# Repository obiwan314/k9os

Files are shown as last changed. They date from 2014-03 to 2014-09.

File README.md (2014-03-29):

k9os
====

A collection of software to control a Raspberry PI based K9 robot.

This is a hardware/software project in progress that is documented on my blog at http://gwfrontiers.blogspot.com.

This project is intended to be checked out on your raspberry pi.
Once this is done run:

cd bin
sudo ./install.sh

This will install the Arduino scripts into the required locations and install and configure the k9os daemon for interfacing over USB to the two arduinos used to control the robot.

This is a personal research project and any sourcecode or hardware designs are provided here without any warrenty or gaurentee.

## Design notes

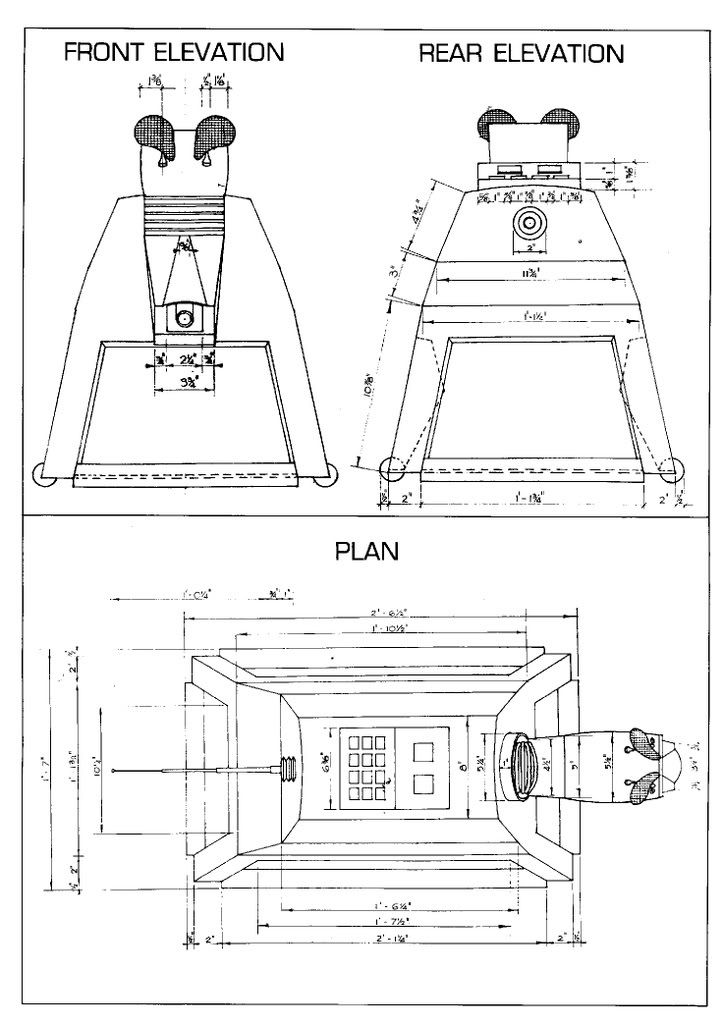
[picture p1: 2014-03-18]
hardware/exterior/k9_views.jpeg

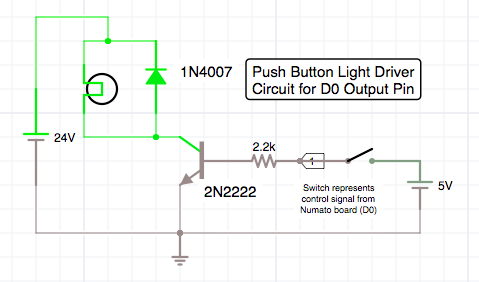
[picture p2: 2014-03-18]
hardware/simulations/light_driver.png

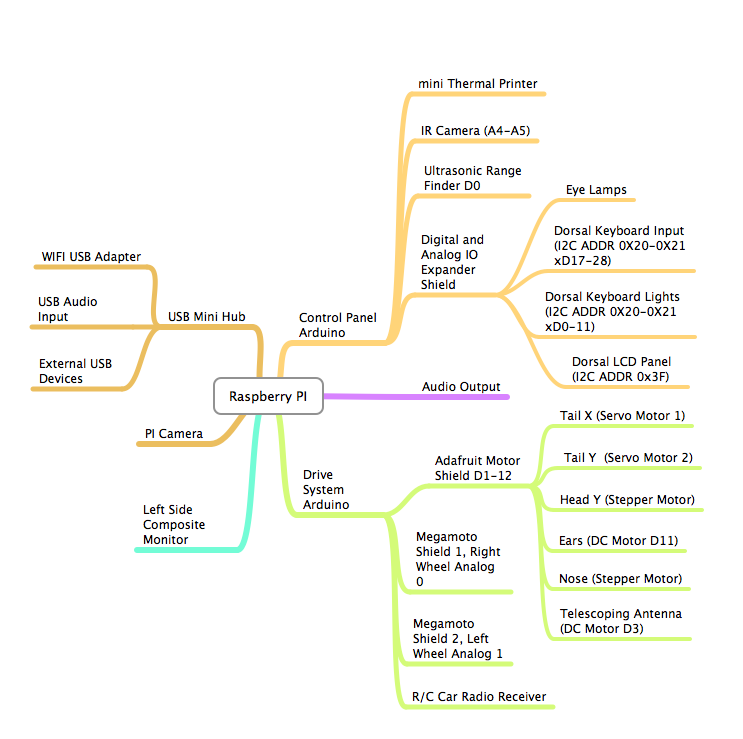
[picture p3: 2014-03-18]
hardware/architecture/system_overview.png

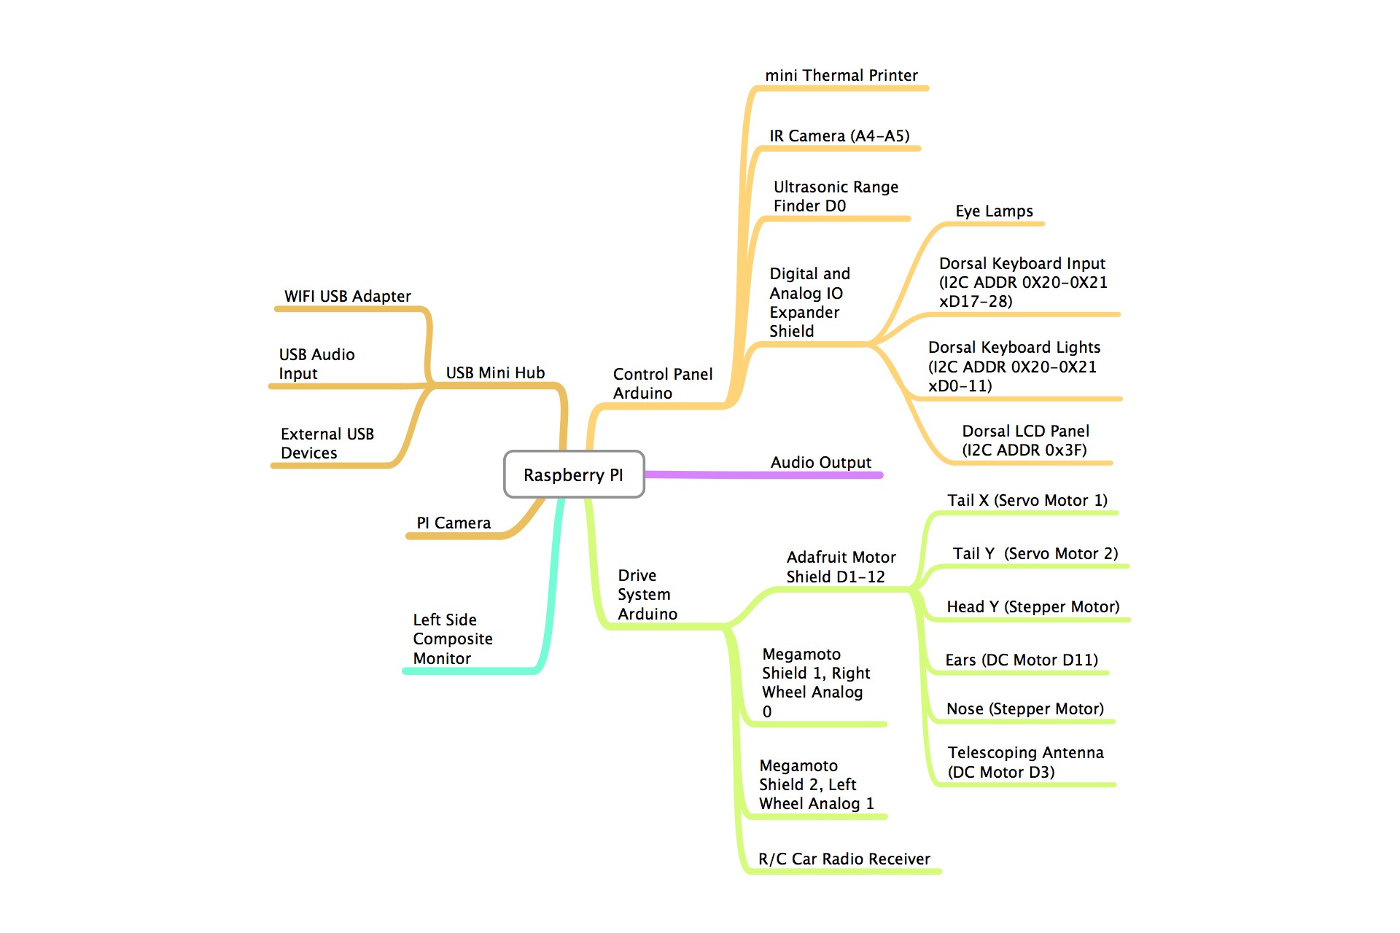
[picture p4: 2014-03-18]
hardware/architecture/system_overview.mindnode/QuickLook/Preview.jpg

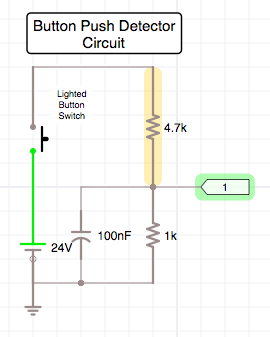
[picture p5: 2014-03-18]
hardware/simulations/switch_controller.png

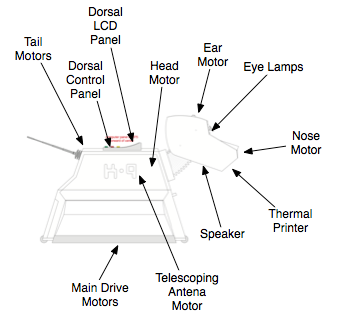
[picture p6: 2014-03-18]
hardware/exterior/right_side.png

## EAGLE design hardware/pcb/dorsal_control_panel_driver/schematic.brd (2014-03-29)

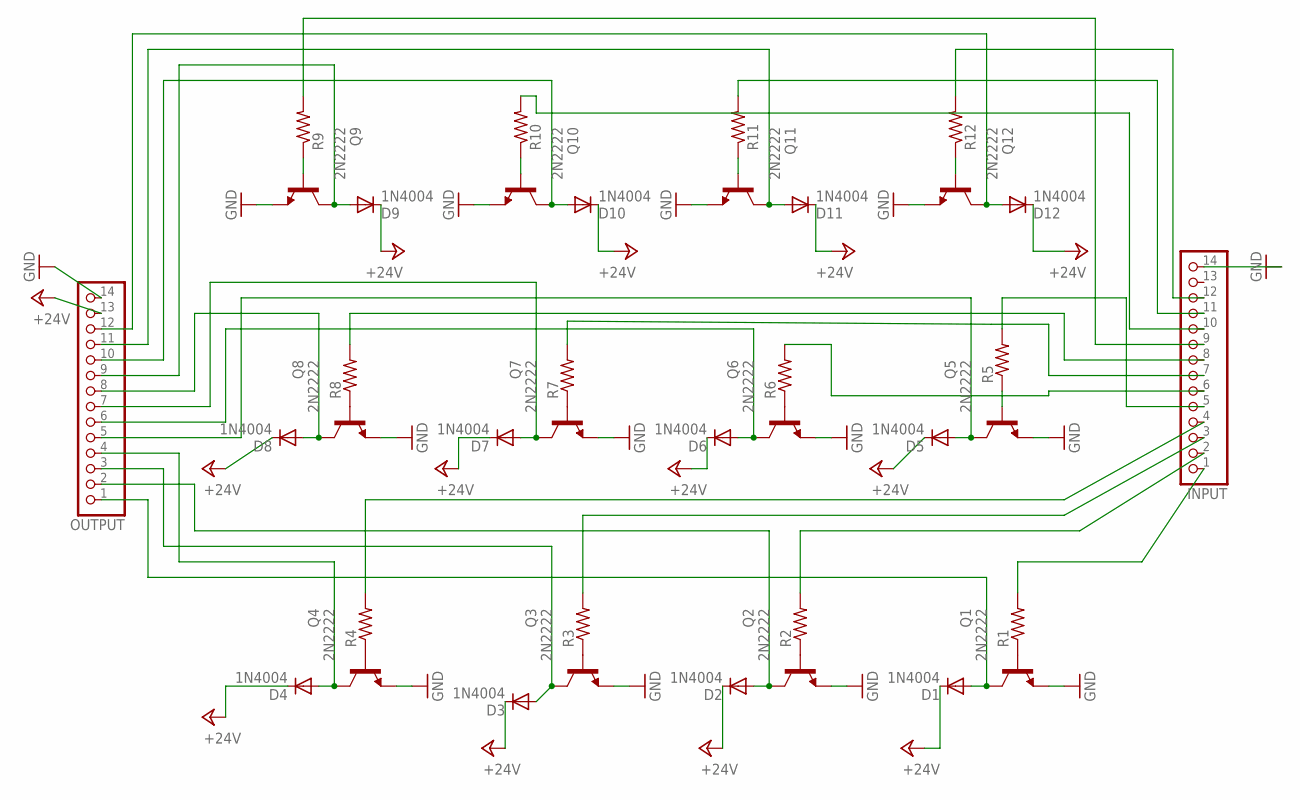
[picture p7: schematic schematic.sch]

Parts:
D1, D2, D3, D4, D5, D6, D7, D8, D9, D10, D11, D12: 1N4004; DO41-10; MPN 1N4004
INPUT: PINHD-1X14; 1X14
OUTPUT: PINHD-1X14; 1X14
Q1, Q2, Q3, Q4, Q5, Q6, Q7, Q8, Q9, Q10, Q11, Q12: 2N2222; TO92-EBC-OVAL; MPN PN2222ATF
R1, R2, R3, R4, R5, R6, R7, R8, R9, R10, R11, R12: R-US_0309/12; 0309/12

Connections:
+24V: D1.C, D2.C, D3.C, D4.C, D5.C, D6.C, D7.C, D8.C, D9.C, D10.C, D11.C, D12.C, OUTPUT.13
GND: INPUT.14, OUTPUT.14, Q1.E, Q2.E, Q3.E, Q4.E, Q5.E, Q6.E, Q7.E, Q8.E, Q9.E, Q10.E, Q11.E, Q12.E
unnamed: D1.A, OUTPUT.1, Q1.C
unnamed: Q1.B, R1.1
unnamed: INPUT.1, R1.2
unnamed: D2.A, OUTPUT.2, Q2.C
unnamed: Q2.B, R2.1
unnamed: INPUT.2, R2.2
unnamed: D3.A, OUTPUT.3, Q3.C
unnamed: Q3.B, R3.1
unnamed: INPUT.3, R3.2
unnamed: D4.A, OUTPUT.4, Q4.C
unnamed: Q4.B, R4.1
unnamed: INPUT.4, R4.2
unnamed: D5.A, OUTPUT.5, Q5.C
unnamed: Q5.B, R5.1
unnamed: INPUT.5, R5.2
unnamed: D6.A, OUTPUT.6, Q6.C
unnamed: Q6.B, R6.1
unnamed: INPUT.6, R6.2
unnamed: D7.A, OUTPUT.7, Q7.C
unnamed: Q7.B, R7.1
unnamed: INPUT.7, R7.2
unnamed: D8.A, OUTPUT.8, Q8.C
unnamed: Q8.B, R8.1
unnamed: INPUT.8, R8.2
unnamed: D9.A, OUTPUT.9, Q9.C
unnamed: Q9.B, R9.1
unnamed: INPUT.9, R9.2
unnamed: D10.A, OUTPUT.10, Q10.C
unnamed: Q10.B, R10.1
unnamed: INPUT.10, R10.2
unnamed: D11.A, OUTPUT.11, Q11.C
unnamed: Q11.B, R11.1
unnamed: INPUT.11, R11.2
unnamed: D12.A, OUTPUT.12, Q12.C
unnamed: Q12.B, R12.1
unnamed: INPUT.12, R12.2

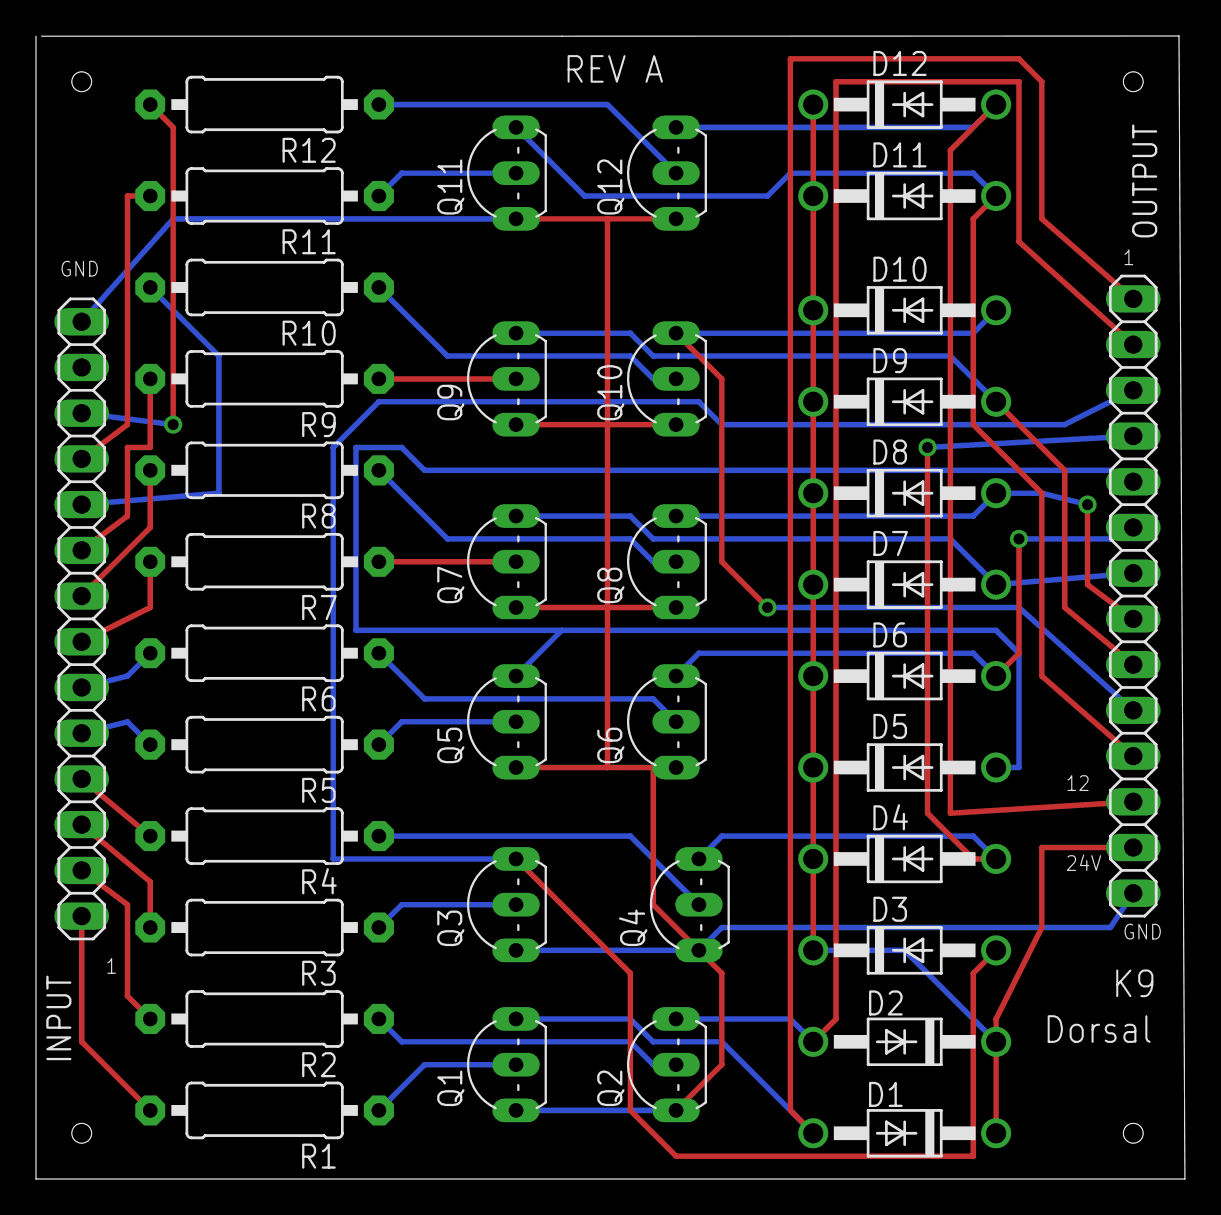
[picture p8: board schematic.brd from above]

Board: 2 copper layers, 63.8 x 63.5 mm, 38 parts (0 on the bottom side), 38 nets.

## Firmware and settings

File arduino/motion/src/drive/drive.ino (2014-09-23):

#include <Servo.h>

/*
 * K9OS drive motor sketch
 * Controls Scooter Motors,
 * Compass, RC Receiver and
 * Ultrasonic Rangefinder
 */

#include <Wire.h> //I2C Arduino Library
#include <math.h>
#include <aJSON.h>

const float pi=3.14159;

// Megamoto Resources
int EnablePin = 8;
int PWMPin = 11;  // Timer2
int PWMPin2 = 3;
int PWMPinA = 9;  // Timer2
int PWMPinA2 = 10;
const int DIRECTION_FORWARD=1;
const int DIRECTION_BACKWARD=-1;
const int DIRECTION_STOP=0;
const int SPEED_STOP=0;
const int SPEED_SLOW=20;
const int SPEED_FAST=40;
const int SPEED_FASTER=60;
const int SPEED_FASTEST=70;
const int SPEED_RIDICULOUS=70;
const int SPEED_LUDICROUS=80;
const int NO_ROTATION=0;
const int LEFT_ROTATION=1;
const int RIGHT_ROTATION=-1;
const int SAFE_DISTANCE=15;

// Compass Constants
const int compassI2CAddress=0x1E;

// Remote Control
const int ultrasonicRangeFinderPin= 4;

// Globals
float lastHeading=-2;
float lastRange=-1;
float persistantBias=0;
int persistantDirection=0;
int persistantSpeed=0;
int persistantRotation=0;
int safetyStop=0;

void setup() {
  // Megamoto
  // initialize the digital pin as an output.
  // Pin 13 has an LED connected on most Arduino boards:
  pinMode(EnablePin, OUTPUT);
  pinMode(PWMPin, OUTPUT);
  pinMode(PWMPin2, OUTPUT);
  pinMode(PWMPinA, OUTPUT);
  pinMode(PWMPinA2, OUTPUT);
  setPwmFrequency(PWMPin, 1);  // change Timer2 divisor to 8 gives 3.9kHz PWM freq
  setPwmFrequency(PWMPinA, 1);  // change Timer2 divisor to 8 gives 3.9kHz PWM freq

  // Remote Control
  pinMode(5, INPUT); // Set our input pins as such
  pinMode(6, INPUT);
  pinMode(7, INPUT);
  pinMode(2, INPUT);

  // Set up compass
  Wire.begin();

  // Put the HMC5883 IC into the correct operating mode
  Wire.beginTransmission(compassI2CAddress); //open communication with HMC5883
  Wire.write(0x02); //select mode register
  Wire.write(0x00); //continuous measurement mode
  Wire.endTransmission();

  Serial.begin(115200); // Establish connection with raspberri pi 115200

}

void loop() {

  processReceivedMessages();
  int currentRange=echoRangeFinder();
  if(abs(lastRange-currentRange)>1){
    Serial.print("{\"onRangeChange\":");
    Serial.print(currentRange);
    Serial.println("}");
    lastRange=currentRange;
  }

  float heading=readHeading();
  if(abs(lastHeading-heading)>=2){
    Serial.print("{\"onHeadingChange\":");
    Serial.print(heading);
    Serial.println("}");
    lastHeading=heading;
  }
  
  processRcTransmitter(currentRange);

}

/**
 * Map RC receiver values to motor control 
 *  actions.
 */
void processRcTransmitter(int currentRange){
  // poll current RC receiver values
  int ch1 = pulseIn(5, HIGH, 25000); // B Switch, Disables everything
  int ch2 = pulseIn(6, HIGH, 25000); // B Stick vertical
  int ch3 = pulseIn(7, HIGH, 25000); // B Stick horizontal
  int ch4 = pulseIn(2, HIGH, 25000); // A Stick horizontal
  float bias=0;

  // Special case, in place rotation
  if(ch2>=1450&&ch2<1500){    
    // throttle at zero
    if(ch4<=1450){ // Spin Left
       controlMotor( 120,DIRECTION_FORWARD,0,LEFT_ROTATION);
       return;
    } else if(ch4>=1500){ // Spin Right
       controlMotor(120,DIRECTION_FORWARD,0,RIGHT_ROTATION);
       return;
    }     
  }
  
  // Calculate current bias
  if(ch4<1500&&ch4>1490)
    bias=0;
  if(ch4<=1490)
    bias=-((ch4-1490)/190.0)*0.8;
  if(ch4>=1500)
    bias=((ch3-1500)/200.0)*0.8;

  
  if(ch1<996){ // This sets SWB as the master motor cut off
      // Master cutoff switch is on or remote is off, autonomous behavior permitted
      if(persistantSpeed>0) {
          // We are moving autonomously
          if(currentRange<SAFE_DISTANCE&&persistantDirection==DIRECTION_FORWARD){
              // Shut down forward motion in from of an obsticle
              controlMotor(0,0,bias,NO_ROTATION);
              if(safetyStop==0){
                 Serial.println("{\"safetystop\":true}");
                 safetyStop=1;
              } 
              return;
          } else {
              // Execute raspberry pi commands if no remote is available and no obsticles present
              controlMotor(persistantSpeed,persistantDirection,persistantBias,persistantRotation);
              return;
          }
      }
   } else {
       // We are in remote control mode
       
       // Reverse
       if(ch2<1400){
          controlMotor(SPEED_FASTER,DIRECTION_BACKWARD,0,NO_ROTATION);
          return;
       }
       if(ch2>=1400&&ch2<1425){
          controlMotor(SPEED_FAST,DIRECTION_BACKWARD,0,NO_ROTATION);
          return;
        }
        if(ch2>=1425&&ch2<1450){
          controlMotor(SPEED_SLOW,DIRECTION_BACKWARD,0,NO_ROTATION);
          return;
        }
        
        // Stop
        if(ch2>=1450&&ch2<1500){
          controlMotor(SPEED_STOP,DIRECTION_STOP,0,NO_ROTATION);
          return;
        }
        
        // Forward
        if(currentRange>SAFE_DISTANCE){
            safetyStop=0;
            if(ch2>=1500&&ch2<1525){
                controlMotor(SPEED_SLOW,DIRECTION_FORWARD,0,NO_ROTATION);
                return;
            }
            if(ch2>=1525&&ch2<1550){
                controlMotor(SPEED_FAST,DIRECTION_FORWARD,0,NO_ROTATION);
                return;
             }
             if(ch2>=1550&&ch2<1575){
                controlMotor(SPEED_FASTER,DIRECTION_FORWARD,0,NO_ROTATION);
                return;
             }
             if(ch2>=1575&&ch2<1600){
                controlMotor(SPEED_FASTEST,DIRECTION_FORWARD,0,NO_ROTATION);
                return;
             }
             if(ch2>=1600&&ch2<1625){
                controlMotor(SPEED_RIDICULOUS,DIRECTION_FORWARD,0,NO_ROTATION);
                return;
             }
             if(ch2>=1625){
                controlMotor(SPEED_LUDICROUS,DIRECTION_FORWARD,0,NO_ROTATION);
                return;
             }
        } else {
              if(safetyStop==0){
                 Serial.println("{\"safetystop\":true}");
                 safetyStop=1;
              } 
             controlMotor(SPEED_STOP,DIRECTION_STOP,0,NO_ROTATION);
        }
  } // end remote control Mode

}

static inline int8_t sgn(int val) {
  if (val < 0) return -1;
  if (val==0) return 0;
  return 1;
}

void controlMotor(int speed,int direction,float bias,int rotate){
  int biasSpeedL=0.0;
  int biasSpeedR=0.0;
  if(bias==0){
    biasSpeedR=speed;
    biasSpeedL=speed;
  } else {
    if(bias*sgn(-direction)>0){
      biasSpeedL=abs(round(speed*bias));
      biasSpeedR=abs(round(speed*(1.0-bias)));
    } else {
      biasSpeedR=abs(round(speed*bias));
      biasSpeedL=abs(round(speed*(1.0-bias)));
    }
  }
//  Serial.print("bias=");Serial.println(bias);
//  Serial.print("Speed=");Serial.println(speed);
//  Serial.print("L=");Serial.println(biasSpeedL);
//  Serial.print("R=");Serial.println(biasSpeedR);
  if(rotate==0){
    if(direction==0){
      // Stop the motor fast
      speed=0;
      analogWrite(PWMPin, 0);
      analogWrite(PWMPinA, 0);
      analogWrite(PWMPin2, 0);
      analogWrite(PWMPinA2, 0);
      digitalWrite(EnablePin, LOW);
    } if(direction>0){
      // Forward
      analogWrite(PWMPin, biasSpeedL);
      analogWrite(PWMPinA, biasSpeedR);
      analogWrite(PWMPin2, 0);
      analogWrite(PWMPinA2, 0);
      digitalWrite(EnablePin, HIGH);
    } else {
      // Backward
      analogWrite(PWMPin, 0);
      analogWrite(PWMPinA, 0);
      analogWrite(PWMPin2, biasSpeedL);
      analogWrite(PWMPinA2,biasSpeedR);
      digitalWrite(EnablePin, HIGH);
    }
  } else {
    // Rotation makes wheels always run in opposite directions
    if(direction==0){
      // Stop the motor fast
      speed=0;
      analogWrite(PWMPin, 0);
      analogWrite(PWMPinA,0);
      analogWrite(PWMPin2, 0);
      analogWrite(PWMPinA2, 0);
      digitalWrite(EnablePin, LOW);
    } if(rotate>0){
      // Left
      //Serial.println("lf");
      analogWrite(PWMPin, 100);
      analogWrite(PWMPinA, 0);
      analogWrite(PWMPin2, 0);
      analogWrite(PWMPinA2,100);
      digitalWrite(EnablePin, HIGH);
    } if(rotate<0) {
      // Backward
      analogWrite(PWMPin, 0);
      analogWrite(PWMPinA,100 );
      analogWrite(PWMPin2,100);
      analogWrite(PWMPinA2,0);
      digitalWrite(EnablePin, HIGH);
    }
  }
}

/*
 * Divides a given PWM pin frequency by a divisor.
 *
 * The resulting frequency is equal to the base frequency divided by
 * the given divisor:
 *   - Base frequencies:
 *      o The base frequency for pins 3, 9, 10, and 11 is 31250 Hz.
 *      o The base frequency for pins 5 and 6 is 62500 Hz.
 *   - Divisors:
 *      o The divisors available on pins 5, 6, 9 and 10 are: 1, 8, 64,
 *        256, and 1024.
 *      o The divisors available on pins 3 and 11 are: 1, 8, 32, 64,
 *        128, 256, and 1024.
 *
 * PWM frequencies are tied together in pairs of pins. If one in a
 * pair is changed, the other is also changed to match:
 *   - Pins 5 and 6 are paired (Timer0)
 *   - Pins 9 and 10 are paired (Timer1)
 *   - Pins 3 and 11 are paired (Timer2)
 *
 * Note that this function will have side effects on anything else
 * that uses timers:
 *   - Changes on pins 5, 6 may cause the delay() and
 *     millis() functions to stop working. Other timing-related
 *     functions may also be affected.
 *   - Changes on pins 9 or 10 will cause the Servo library to function
 *     incorrectly.
 *
 * Thanks to macegr of the Arduino forums for his documentation of the
 * PWM frequency divisors. His post can be viewed at:
 *   http://www.arduino.cc/cgi-bin/yabb2/YaBB.pl?num=1235060559/0#4
 */

void setPwmFrequency(int pin, int divisor) {
  byte mode;
  if(pin == 5 || pin == 6 || pin == 9 || pin == 10) { // Timer0 or Timer1
    switch(divisor) {
      case 1: mode = 0x01; break;
      case 8: mode = 0x02; break;
      case 64: mode = 0x03; break;
      case 256: mode = 0x04; break;
      case 1024: mode = 0x05; break;
      default: return;
    }
    if(pin == 5 || pin == 6) {
      TCCR0B = TCCR0B & 0b11111000 | mode; // Timer0
    } else {
      TCCR1B = TCCR1B & 0b11111000 | mode; // Timer1
    }
  } else if(pin == 3 || pin == 11) {
    switch(divisor) {
      case 1: mode = 0x01; break;
      case 8: mode = 0x02; break;
      case 32: mode = 0x03; break;
      case 64: mode = 0x04; break;
      case 128: mode = 0x05; break;
      case 256: mode = 0x06; break;
      case 1024: mode = 0x7; break;
      default: return;
    }
    TCCR2B = TCCR2B & 0b11111000 | mode; // Timer2
  }
}

float echoRangeFinder() {
  pinMode(ultrasonicRangeFinderPin, OUTPUT);          // Set pin to OUTPUT
  digitalWrite(ultrasonicRangeFinderPin, LOW);        // Ensure pin is low
  delayMicroseconds(2);
  digitalWrite(ultrasonicRangeFinderPin, HIGH);       // Start ranging
  delayMicroseconds(5);              //   with 5 microsecond burst
  digitalWrite(ultrasonicRangeFinderPin, LOW);        // End ranging
  pinMode(ultrasonicRangeFinderPin, INPUT);           // Set pin to INPUT
  int duration = pulseIn(ultrasonicRangeFinderPin, HIGH); // Read echo pulse
  float inches = duration / 74 / 2;        // Convert to inches
  //Serial.println(inches);            // Display result
  return inches;
}

float readHeading(){
  int x,y,z; //triple axis data

  //Tell the HMC5883 where to begin reading data
  Wire.beginTransmission(compassI2CAddress);
  Wire.write(0x03); //select register 3, X MSB register
  Wire.endTransmission();

  //Read data from each axis, 2 registers per axis
  Wire.requestFrom(compassI2CAddress, 6);
  if(6<=Wire.available()){
    x = Wire.read()<<8; //X msb
    x |= Wire.read(); //X lsb
    z = Wire.read()<<8; //Z msb
    z |= Wire.read(); //Z lsb
    y = Wire.read()<<8; //Y msb
    y |= Wire.read(); //Y lsb
  }
//  Serial.print(x);
//    Serial.print("\t");
//      Serial.println(y);
//    Serial.print(",");
//        Serial.println(z);
  int cy=-330;
  int cx=33;

  int dy=y-cy;
  int dx=x-cx;
//    Serial.print("dx,dy=");
//    Serial.print(dx);
//    Serial.print(",");
//        Serial.println(dy);
  float ratio=(float)dy/(float)dx;
//    Serial.print("Ratio=");
//        Serial.println(ratio);
  float rawAngle=abs(atan(ratio)*180.0/pi);
  if(dx>0&&dy<=0){
    //Serial.println("+-");
    return 360-rawAngle;
  }
  if(dx<=0&&dy<=0){
    //Serial.println("--");
    return rawAngle+180;
  }
  if(dx<=0&&dy>0){
    //Serial.println("-+");
    return 180-rawAngle;
  }
  if(dx>0&&dy>0){
    //Serial.println("++");
    return rawAngle;
  }

}

int readline(int readch, char *buffer, int len){

  static int pos = 0;
  int rpos;

  if (readch > 0) {

    switch (readch) {
      case '\r':
        rpos = pos;
        pos = 0;  // Reset position index ready for next time
        return rpos;
      default:
        if (pos < len-1) {
          buffer[pos++] = readch;
          buffer[pos] = 0;
        }
    }
  }
  // No end of line has been found, so return -1.
  return -1;
}

void processMessage(aJsonObject *msg){
    aJsonObject  *rotate = aJson.getObjectItem(msg, "rotate");
    aJsonObject  *goforward = aJson.getObjectItem(msg, "goforward");
    aJsonObject  *gobackward = aJson.getObjectItem(msg, "gobackward");
    aJsonObject  *stopnow = aJson.getObjectItem(msg, "stop");

   if (rotate->type == aJson_String) {
      String direction=(String(rotate->valuestring));
      float bias=0;
      if(direction.equals("LEFT")){
        persistantSpeed=SPEED_FAST;
        persistantDirection=DIRECTION_FORWARD;
        persistantBias=0.5;
        persistantRotation=LEFT_ROTATION;
      } else {
        persistantSpeed=SPEED_FAST;
        persistantDirection=DIRECTION_FORWARD;
        persistantBias=-0.5;
        persistantRotation=RIGHT_ROTATION;
      }
      Serial.println("{\"response\":\"OK rotate\"}");
      return;
    }
    if (goforward->type == aJson_Int) {
      int aspeed=goforward->valueint;
      persistantSpeed=aspeed;
      persistantDirection=DIRECTION_FORWARD;
      persistantBias=0;
      persistantRotation=NO_ROTATION;
      Serial.println("{\"response\":\"OK goforward\"}");
      return;
    }

    if (gobackward->type == aJson_Int) {
      int aspeed=gobackward->valueint;
      persistantSpeed=aspeed;
      persistantDirection=DIRECTION_BACKWARD;
      persistantBias=0;
      persistantRotation=NO_ROTATION;
     Serial.println("{\"response\":\"OK gobackward\"}");
     return;
    }

    if (gobackward->type == aJson_String) {
      //lcd.print(String(line3->valuestring));
      persistantSpeed=SPEED_FAST;
      persistantDirection=DIRECTION_BACKWARD;
      persistantBias=0;
      persistantRotation=NO_ROTATION;
     Serial.println("{\"response\":\"OK gobackward\"}");
     return;
    }

    if (stopnow->type == aJson_True) {
      float bias=0;
      controlMotor(0,DIRECTION_STOP,bias,NO_ROTATION);
      persistantSpeed=SPEED_STOP;
      persistantDirection=DIRECTION_STOP;
      persistantBias=0;
      persistantRotation=NO_ROTATION;
      Serial.println("{\"response\":\"OK stop\"}");
      return;

    }
    Serial.println("{\"response\":\"ERROR unknown\"}");
}

void processReceivedMessages(){
    static char buffer[200];
    if (readline(Serial.read(), buffer, 200) > 0) {
        Serial.println(buffer);
        aJsonObject *msg = aJson.parse(buffer);
        processMessage(msg);
        aJson.deleteItem(msg);
    }
}

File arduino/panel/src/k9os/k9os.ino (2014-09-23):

/**
 * K9 OS v1.0
 *
 */
#include <Wire.h>
#include <LCD.h>
#include <LiquidCrystal_I2C.h>
#include <aJSON.h>
#include <Servo.h>

#define I2C_ADDR    0x3F  // Define I2C Address where the PCF8574A is
#define BACKLIGHT_PIN     3
#define En_pin  2
#define Rw_pin  1
#define Rs_pin  0
#define D4_pin  4
#define D5_pin  5
#define D6_pin  6
#define D7_pin  7
byte U4PortAP=0, U4PortBP=0, U4PortA=0, U4PortB =0; // Define variables to hold I/O port readings.
int testModeCounter=0;
int n = 1;
int debug=0;
int testmodeStatus=0;
unsigned long last_print = 0;
//aJsonStream serial_stream(&Serial);
LiquidCrystal_I2C lcd(I2C_ADDR,En_pin,Rw_pin,Rs_pin,D4_pin,D5_pin,D6_pin,D7_pin);
int pattern=0;
Servo myservoVertical;  // create servo object to control a servo
Servo myservoHorizontal;
int pos = 0;    // variable to store the servo position
int wag=0;
void setup()
{
  setTailToNeutral();
  lcd.begin (20,4);
  
  // Switch on the backlight
  lcd.setBacklightPin(BACKLIGHT_PIN,POSITIVE);
  lcd.setBacklight(HIGH);
  lcd.home ();                   // go home

  lcd.print(" *** K9 OS 0.1a *** ");  
  lcd.setCursor ( 0, 1 );        // go to the 2nd line
  lcd.print("   SYSTEM BOOTING    ");
  lcd.setCursor ( 0, 2 );        // go to the third line
  lcd.print("    PLEASE WAIT");
  lcd.setCursor ( 0, 3 );        // go to the fourth line
  lcd.print("");
  
  // Setup Serial Communications
  Serial.begin(115200);
  setupKeypad();
  
}


void setupKeypad()
{
   Wire.begin();                                  // Begin I2C bus
   /* 
    *  The following code starts I2C communication with MCP23017(U2).Please refer MCP23017 datasheet
    *  for register addresses. Sets all GPIOs of this IC to OUTPUT 
    */
   Wire.beginTransmission(0x20);                  // Starts communication with MCP23017(U2) IC
   Wire.write(0x00);                              // Set MCP23017 memory pointer to IODIRA address
   Wire.write(0x00);                              // Set all pins of PORTA to outputs
   Wire.endTransmission();                        // Ends I2C communication with MCP23017(U2) IC

   Wire.beginTransmission(0x20);                  // Starts communication with MCP23017(U2) IC
   Wire.write(0x01);                              // Set MCP23017 memory pointer to IODIRB address
   Wire.write(0x00);                              // Set all pins of PORTB to outputs
   Wire.endTransmission();                        // Ends I2C communication with MCP23017(U2) IC

   /* 
    *  The following code starts I2C communication with MCP23017(U4).Please refer MCP23017 datasheet
    *  for register addresses. Sets all GPIOs of this IC to OUTPUT 
    */
   Wire.beginTransmission(0x21);                  // Starts communication with MCP23017(U4) IC
   Wire.write(0x00);                              // Set MCP23017 memory pointer to IODIRA address
   Wire.write(0xFF);                              // Set all PORTA pins to OUTPUT
   Wire.endTransmission();                        // Ends I2C communication with MCP23017(U4) IC

   Wire.beginTransmission(0x21);                  // Starts communication with MCP23017(U4) IC
   Wire.write(0x01);                              // Set MCP23017 memory pointer to IODIRB address
   Wire.write(0xFF);                              // Set all PORTB pins to OUTPUT
   Wire.endTransmission();                        // Ends I2C communication with MCP23017(U4) IC
   DigitalIO(0);
}

void clearlcdnow(){
//  lcd.setCursor ( 0, 0 );
//  lcd.print("                    ");
  lcd.setCursor ( 0, 1 );
  lcd.print("                    ");
  lcd.setCursor ( 0, 2 );
  lcd.print("                    ");
  lcd.setCursor ( 0, 3 );
  lcd.print("                    ");
}

void sendKeyboardEvents(byte a, byte ax,byte b,byte bx){
  String response="";
  if((bx&1)==1){
    if((b&1)==1){
      response=response+"\"key1\":\"down\",";  
    } else {
      response=response+"\"key1\":\"up\",";  
    }  
  }
  if((bx&2)==2){
    if((b&2)==2){
      response=response+"\"key2\":\"down\",";  
    } else {
      response=response+"\"key2\":\"up\",";  
    }  
  }
  if((bx&4)==4){
    if((b&4)==4){
      response=response+"\"key3\":\"down\",";  
    } else {
      response=response+"\"key3\":\"up\",";  
    }  
  }
  if((bx&8)==8){
    if((b&8)==8){
      response=response+"\"key4\":\"down\",";  
    } else {
      response=response+"\"key4\":\"up\",";  
    }  
  }
  if((bx&16)==16){
    if((b&&16)==16){
      response=response+"\"key5\":\"down\",";  
    } else {
      response=response+"\"key5\":\"up\",";  
    }  
  }
  if((bx&32)==32){
    if((b&32)==32){
      response=response+"\"key6\":\"down\",";  
    } else {
      response=response+"\"key6\":\"up\",";  
    }  
  }
  if((bx&64)==64){
    if((b&64)==64){
      response=response+"\"key7\":\"down\",";  
    } else {
      response=response+"\"key7\":\"up\",";  
    }  
  }
  if((bx&128)==128){
    if((b&128)==128){
      response=response+"\"key8\":\"down\",";  
    } else {
      response=response+"\"key8\":\"up\",";  
    }  
  }
  if((ax&16)==16){
    if((a&16)==16){
      response=response+"\"key9\":\"down\",";  
    } else {
      response=response+"\"key9\":\"up\",";  
    }  
  }
  if((ax&32)==32){
    if((a&32)==32){
      response=response+"\"key10\":\"down\",";  
    } else {
      response=response+"\"key10\":\"up\",";  
    }  
  }
  if((ax&64)==64){
    if((a&64)==64){
      response=response+"\"key11\":\"down\",";  
    } else {
      response=response+"\"key11\":\"up\",";  
    }  
  }
  if((ax&128)==128){
    if((a&128)==128){
      response=response+"\"key12\":\"down\",";  
    } else {
      response=response+"\"key12\":\"up\",";  
    }  
  }
  
  response="{"+response.substring(0, response.length() - 1)+"}";
  Serial.println(response);

}
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

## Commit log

2014-03-29 Added Eagle PCB files
    [schematic.brd, schematic.sch]
2014-03-29 Moved PCB layout files into their own folder
    [schematic.brd, schematic.sch]
2014-04-06 Drive now operates all motors, the ultrasonic sensor and the compass
2014-04-06 Debugging- sketch now runs motor continuosly
2014-04-07 Added support for Raspberry PI remote control.
2014-04-08 Added motor wiring diagram
2014-07-12 Installed tail servos and added support to trigger them.
2014-09-23 Printer support
